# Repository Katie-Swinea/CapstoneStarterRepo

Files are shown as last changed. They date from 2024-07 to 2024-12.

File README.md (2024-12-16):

# Paper Wad Interceptor - Purple Team

## Executive Summary

It is a common problem that students that are currently in school lack interest in STEM subjects. This is a problem for society as it hinders innovation and
discovery in future generations. It also negatively affects current infrastructure and systems in place. Without students who are interested in these fields
of study and existing structures, failures in infrastructure and government programs could occur. This project aims to spark students interest in STEM
fields and applying the principles to existing infrastructure.

The goal of this project is to replicate a missile defense system to interest children in STEM, specifically the department of defense. This is done be
scaling the original problem down to a smaller area. This scale down is proposed as a paper wad interceptor in a classroom. However, this project is
incredibly ambitious for the time provided to the team. Due to this, the project was then simplified further. Instead of a paper wad that could come from
anywhere in a large classroom, the object being tracked was replaced with a plastic practice golf ball. The golf ball will be coming from a structure with
fifteen possible start point and two variable heights. The narrows down the possible trajectories to 30. The space was also contained to a 64 inch by 78
inch rectangle. This resulted in a project focused on small object tracking with the added challenge of the object's material properties and speed. Since
the project was already being scaled down, the project was also turned into a competition between two teams. 

## Capabilities

This system is able to accurately detect, track, and aim at the incoming golfballs on the gameboard. It has been designed to mitigate false detections as much as possible. It is able to accurately intercept the
ball a significant percent of the time.

## Salient Outcomes

The team has learned about tracking smaller objects through this project. The object's size was not an issue the team anticipated to be such a challenge.
While there are several sensors that are capable of tracking objects, very few can reliably track a small object such as a plastic golf ball. This issue was
highlighted even further with the limitation sensors that can detect plastic. Research shows that vision detection is the most reliable and used technology
for small object tracking. This was an outcome the team was not expecting from the project. This difficulty was something the team had to overcome and learn
from to achieve the goal of the project.

## Project Demonstration & Images

The experimental analysis of this repository has several pictures of the capabilities of this project. The final presentation also has a video of the interceptor tracking and hitting the golfball.

## About Us

### Team

Garrett Armstrong: Electrical Engineering major who focused on the power for the system created.

Savannah Metlzer: Electrical Engineering major who focused on providing the signal conversions and aiming coordinates for the motors.

Jonathan Neal: Electrical Engineering major who focused on interfacing the extra lights and sound into the system.

Finlay Patoto: Computer Engineering major who focused on the processor and basic mathmatical calculations from the sensor data.

Katie Swinea: Computer Engineering major who focused on the computer vision algorithms to detect the object and convey the sensor data.

Kevin Ulrich: Computer Engineering major who focused on the research and calibration of a sensor to detect the object.

### Faculty Supervisor

The team's faculty supervisor was Dr. Jesse Roberts. The team's supervisor then became Micah Rentschler for the second semester.

### Stakeholders

The customer is Devcom who also created and proposed the project and competition.

### Recognitions

The team wants to acknowledge the contributions of the partnered Mechanical Engineering team. The team consists of: Ishak Lamei, Samuel Rainey, Steven
Tucker, and Austin Williams. The team would also like to thank Cooper Nelson for helping the team test different sensor options before ordering, Ethan Dixon who was a source of moral support through out the
project, and Adam Morrow who was on the other team, but helped us finish construction of the gameboard and let us bounce ideas off of him.

## Repo Organization

The timeline that was used as a template for the team's more detailed timeline and this README are present in main with the following repository.

### Reports

This repository contains the original Project Proposal, the revised Proposal, the Conceptual Design and Planning draft, and the final Conceptual Design and
Planning document. All of these files are included as pdf documents. There are also several markdown files containing instructions for furture documents. 
These include the Lessons Learned and Acquired, Experimentation, Final Presentation, and Poster Documents. Lastly, there is another repository called Poster
Template present.

### Documentation

This repository contains several repositories inside of it. One is 3D models which will include all the final designs for 3D models. Next is Electrical which
contains two repositories called PCB and Schematics. PCB will house all final PCB designs. Schematics will house all final designs for wiring schematics. The
Images repository is used to store the images of the final project. The team has also used this repository to house all images used in documentation. Meeting
Minutes are included in a repository here as well. Signoffs contains the approved final design of each subsystem. 

### Software

This repository contains the necessary software and designed software for the project. All of theses softwares are already uploaded to the appropriate hardware.

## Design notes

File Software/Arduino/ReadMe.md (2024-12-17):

# Code for the Arduino

This is the code that was developed for the competition. It is used to control the stepper motors in order to position and aim the interceptor towards the incoming 
golfball. It uses the information from the jetson nano sent via I2C communication. The information is a byte that contains the x and y position for the motors and a 
fire bit for the solenoid to launch the projectile at the golfball.

This software uses header files ezButton.h, AccelStepper.h, Wire.h, and avr/wdt.h for proper interfacing with the stepper motors, limit switches, and solenoid to 
ensure the interceptor moves properly.

This software can be uploaded on the adruino by connecting it to a computer with the code and uploading it when the adruino is ready to accept a new upload of code. 
Ensure the arduino and computer are connected to the same ground. This version of the code is currently uploaded on the arduino.

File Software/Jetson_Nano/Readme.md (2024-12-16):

# Code for the Jetson Nano

This is the code that was developed for the competition. It includes the integration of the jetson nano with the real sense camera including the color map and paramter
adjustments. The code also includes the image processing, false detection handling, frame storage, velocity and acceleration calculations, and trajectory predictions.
The location of the ball and predictions are sent to arduino via I2C. The code also include the buzzer noise for firing and light's pattern and the pause switch
functionality with the switches input into the nano being used to temporarily stop the program.

The code uses the opencv library, the real sense library, and the jestson's gpio pin interface. It also requires other libraries for functionality like the time, 
numpy, typing for tuple, subprocess, sys, threading, os, smbus2, time, and math. These are used for specfic operations and calculations.

This software can be uploaded on the jeston nano via a USB as it it. It can be set to run when the jetson nano is turned on with a simple program already uploaded on
the jeston nano. Use a monitor to see the jeston nano console and change the program that runs on start up.

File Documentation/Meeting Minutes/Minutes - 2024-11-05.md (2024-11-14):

# Capstone II Team 5 Week 11 (11/04 – 11/08)

### 11/05 @ 11:00 AM – 11:48 AM

### Attendance: Everyone + DEVCOM + Mechanicals

## Updates:

Garrett: Finished experimental analysis for power system

Finn: Started testing values for lookup tables

Katie: Refined image detection to reduce noise and verified correct communication with code elsewhere on Jetson.

Ross: Fixed buzzer

Savannah: Started testing values for lookup tables

Kevin: Helped find fix for dart jamming problem

## Future Tasks:

Garrett: Work on lookup tables for converting coordinates from camera to real life.

Finn: Work on lookup tables for converting coordinates from camera to real life.

Katie: Work on lookup tables for converting coordinates from camera to real life.

Ross: Finish experimental analysis for extra system

Savannah: Work on experimental analysis for arduino system

Kevin: Work on experimental analysis for camera system

## Discussions/Decisions:

Discussed other team's sensor posts and talked about the 6 foot rule for our team.

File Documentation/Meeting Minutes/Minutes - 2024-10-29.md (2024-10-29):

# Capstone II Team 5 Week 10 (10/28 – 11/1)

### 10/29 @ 11:30 AM – 12:06 PM

### Attendance: Everyone

## Updates:

Garrett: Completed housing.

Finn: Developed working prototype of calculations for coordinates for aiming.

Katie: Worked with image detection to further reduce noise.

Ross: Worked on integration of buzzer.

Savannah: Finished wiring up gameboard

Kevin: Remounted camera to the front to avoid image detection noise from gun.

## Future Tasks:

Garrett: Continue writing drafts of final reports.

Finn: Continue developing the calculations code with jetson.

Katie: Continue refining image detection to reduce noise and verify correct communication with code elsewhere on Jetson.

Ross: Continue fixing buzzer.

Savannah: Work on converting coordinates from image detection to real life coordinates with aiming turret.

Kevin: Help develop code for calculations and image detection.

## Discussions/Decisions:

Discussed progress and verified future tasks to continue finishing up subsystems for minimal functioning prototype.

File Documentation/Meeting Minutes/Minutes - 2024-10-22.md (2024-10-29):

# Capstone II Team 5 Week 9 (10/21 – 10/25)

### 10/22 @ 11:00 AM – 11:46 AM

### Attendance: Everyone + Mechanicals + DEVCOM

## Updates:

Garrett: Helped finalize wiring in finished housing.

Finn: Helped finalize wiring in finished housing. Also worked with aiming code and positioning.

Katie: Fixed image detection noise problem.

Ross: Helped finalize wiring in finished housing.

Savannah: Worked on the gameboard.

Kevin: Taped out the positions of sensor posts and other important positions on the gameboard. Camera mount finished

## Future Tasks:

Garrett: Start writing paper for experimental analysis and final paper.

Finn: Work on calculation with coordinates from image detection.

Katie: Refine image detection with testing.

Ross: Integrate buzzer into housing and the rest of the subsystems.

Savannah: Finish the setup of the gameboard. (Stringing up the rest of the wires and reset the anchor points for the wires to set in.

Kevin: Determine final position of the camera.

## Discussions/Decisions:

Discussed progress with mounting, housing, Arduino code, Jetson code, timing, and optimization. Also discussed possibility of the removal of the 6-foot rule. talked about making a compromise package for the other team. Verified that there are no changes to the gameboard.

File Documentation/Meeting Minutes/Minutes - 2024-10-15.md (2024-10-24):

# Capstone II Team 5 Week 8 (10/14 – 10/18)

### 10/15 @ 11:00 AM – 11:27 AM

### Attendance: Everyone

## Updates:

Garrett: Finalized wiring within the housing.

Finn: Launcher fires and aims with arduino through Jetson nano.

Katie: Further implemented the multiframe storage for image detcection.

Ross: Finished layout of internal units and attached to base of housing.

Savannah: Helped with arduinos firing with communication with Jetson.

Kevin: Waiting for housing and camera mount to be completed.

## Future Tasks:

Garrett: Waiting for mechanicals to finish walls of housing.

Finn: Fine tune the aiming code.

Katie: Fix image detection noise problem.

Ross: Waiting for mechanicals to finish walls of housing.

Savannah: Help fine tune the aiming code and finalize gameboard.

Kevin: Waiting for mechanicals to finish walls and camera mount.

## Discussions/Decisions:

Discussed and set deadlines for remaining tasks till end of semester.

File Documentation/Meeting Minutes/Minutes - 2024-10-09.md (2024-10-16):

# Capstone II Team 5 Week 7 (10/07 – 10/11)

### 10/09 @ 11:00 AM – 11:43 AM

### Attendance: Everyone + Mechanicals + DEVCOM

## Updates:

Garrett: Finalized wiring between different subsystems.

Finn: Jetson is now communicating with arduinos.

Katie: Began implementation of multiframe storage.

Ross: Finalized mapping out systems into the housing.

Savannah: Helped communication between arduinos and Jetson.

Kevin: Recieved USB C cable.

## Future Tasks:

Garrett: Wired different systems together through the housing.

Finn: Get launcher to fire with the arduinos.

Katie: Finish multiframe storage and prepare for testing.

Ross: Put housing together.

Savannah: Help get launcher to fire with arduinos.

Kevin: Discuss camera mount with mechanicals.

## Discussions/Decisions:

Discussed with DEVCOM some questions regarding the gameboard and clearing up some finer details and misunderstandings.

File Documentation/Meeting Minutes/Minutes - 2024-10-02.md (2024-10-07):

# Capstone II Team 5 Week 5 (10/30 – 10/04)

### 10/02 @ 11:00 AM – 11:32 AM

### Attendance: Everyone + Mechanicals

## Updates:

Garrett: Mapped out subsystems within 1 cubic foot box.

Finn: Researched communication protocols for link between Jetson and arduino

Katie: Determined method for testing timing and gathering frame data.

Ross: Mapped out subsystems within 1 cubic foot box.

Savannah: Helped mechanicals swap from their arduino to our arduino

Kevin: Helped map out subsystems within 1 cubic foot box.

## Future Tasks:

Garrett: Continue mapping out subsystems in box. Ordered new parts for mechanical subsystem change.

Finn: Implement communication with arduinos.

Katie: Implement multi-frame data storing. Start testing actual timing processes.

Ross: Continue mapping out subsystems in box.

Savannah: Help implement communication with Jetson.

Kevin: Submit BOM for new, longer usb c cable.

## Discussions/Decisions:

Discussed housing layouts for fitting each subsystem into required space.

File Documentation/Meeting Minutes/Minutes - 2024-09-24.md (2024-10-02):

# Capstone II Team 5 Week 5 (9/23 – 9/27)

### 09/24 @ 11:00 AM – 11:45 AM

### Attendance: Everyone + DEVCOM + Mechanicals

## Updates:

Garrett: Fully integrated with each subsystem besides mechanical.

Finn: Worked on integration with buzzer, pause switch, and auto-launching scripts.

Katie: Reexamined image detection plan (performance, timing, etc.)

Ross: Helped integrate extras system with power and jetson.

Savannah: Got Arduino in.

Kevin: Helped with integration with extras subsytem and jetson nano.

## Future Tasks:

Garrett: Start configuring layout for fitting everything together.

Finn: Integrate with the rest of the subsystems and start configuring layout.

Katie: Continue working on more exact timing for the image detection.

Ross: Start configuring layout for fitting everything together.

Savannah: Work with mechanicals to integrate between launcher and jetson.

Kevin: Help configure layout for camera subsystem

## Discussions/Decisions:

Talked with DEVCOM about image detection progress and developments. Also discussed game board changes such as the fishing hook for sliding down the fishing line better.

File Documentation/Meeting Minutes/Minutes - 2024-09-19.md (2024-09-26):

# Capstone II Team 5 Week 4 (9/16 – 9/20)

### 9/19 @ 11:30 AM – 12:00 PM

### Attendance: Everyone

## Updates:

Garrett: Started wiring and troubleshooting power subsystem.

Finn: Got current image detection script working with camera and jetson nano

Katie: 

Ross: Assembled extras and pause switch subsystem.

Savannah: Submitted BOM and talked with mechanicals to figure out how to integrate with the rest of the subsystems.

Kevin: Helped get current image detection working off of Jetson Nano and camera.

## Future Tasks:

Garrett: Continue assembling power subsystem and start integration testing.

Finn: Get Jetson Nano to auto run scripts and show status.

Katie: Plan timelines for internal deadlines to ensure all subsystems are getting integrated on time.

Ross: Integrate extras subsystem with power subsystem and Jetson.

Savannah: Waiting on parts.

Kevin: Help integrate Jetson with other subsystems.

## Discussions/Decisions:

Discussed housing and made sure all subsystems would fit within the specs and constraints of the rules and what the mechanicals are working on.

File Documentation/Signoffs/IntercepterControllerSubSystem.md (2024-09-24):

# Interceptor Controller Subsystem

## **Function:**
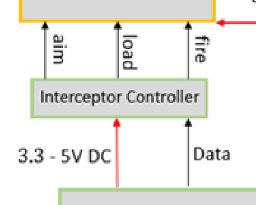
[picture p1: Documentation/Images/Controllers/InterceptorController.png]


Figure 1: Interceptor Controller Subsystem

The goal of this subsystem is to activate the position motors and firing mechanism within the mechanical system, maintain safe firing speed, as well as alleviate some of the coding within the processor. 

## **Constraints:**

|No.|Constraint|Origin|
|--|---|---|
|1|The Interceptor Controller shall move firing mechanism to 1 of 30 pre set locations |Conceptual Design|
|2|Must communicate with processor| Conceptual Design |
|3|Shall receive 5V power supply from processor| Conceptual Design|
|4|Must change direction of the motors in the Mechanical's section |Conceptual Design|
|5|Must maintain safe firing speed and distance|Conceptual Design/Rule Book|
|6|Must change position before incoming object enters the "kill zone"| Conceptual Design|

1.	Using the sensor data analyzed by the processor the arduino activates the 2 position motors to move to 1 of 30 set positions.
2.	After completing the movement to the desired position, and the projectile is within set "kill zone", the firing mechanism is engaged firing only one shot.
3.	Using the 5V pin on the processor to power the adruino.
4.  To be able to move to the correct coordinates the motors need to move in either direction along the x and y axis.
5.  Per Devcom rule books the projectile must be fired at a safe speed and stay within a distance of 6ft *this speed will be found by the ME team*
6.  Based off calculations made with the dimensions of the game board it will take the projectile approximately 1.95 seconds to 7.4 seconds to travel down the line given the two different height points. However, after subtracting the worst-case scenario with sensing, processing, and travel time this leaves 1.6 seconds for the firing mechanism to move into position and fire at the object before collision.

## **Buildable Schematics:**

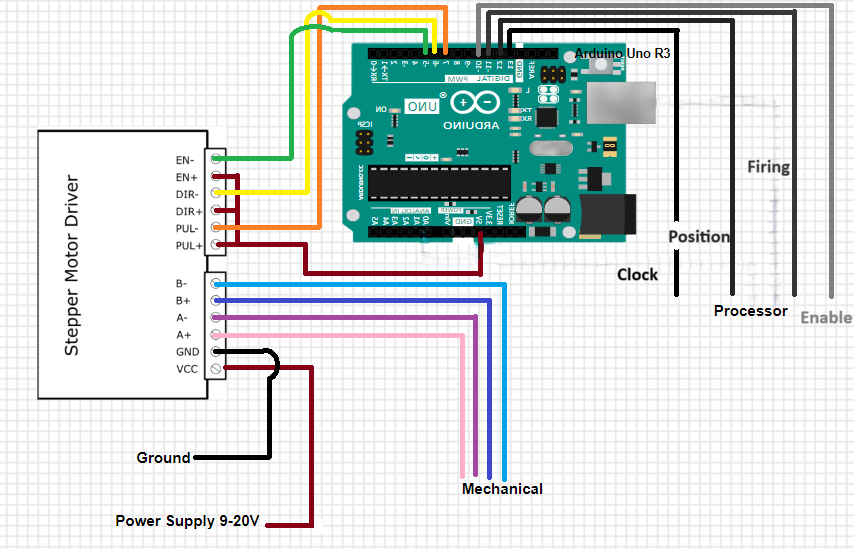
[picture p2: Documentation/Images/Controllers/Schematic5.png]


Figure 2: Buildable Schematic

## **Analysis:**

Stepper Motor Integration:

The stepper motor driver converts a pulse signal into a precise position and can also make the rotation of the motor bidirectional. With this function and the orientation of the motors we are able to create an x and y axis for the firing mechanism to move on. This allows 30 set coordinates to be programmed for possible incoming attacks. This component was pick by the Mechanical Engineering portion of our team, however, it is important to this subsystem because of its direct integration within the Arduino. Through GPIO communication, as stated above, the Arduino UNO R3 commands the stepper motor driver to adjust the interceptor's position, aligning it with the golf ball's predicted path. Real-time trajectory data calculated by the processor is sent to the Arduino that will guide its precise motor movements, ensuring accurate interception. After firing is completed the stepper motor will be put back into a zero position. While it is in its zero position, the processor can count how many steps the motor takes to determine the correct aiming position [6].

Arduino Intergration:

*Motor Integration*

As stated before the stepper motor drive given was picked by the ME team. This component was picked through testing and consideration of use by them. The Arduino UNO R3 seamlessly integrates with the TB6600 Stepper Motor Driver to control the interceptor's aiming mechanism [7]. With that being said an Arduino was picked to be used within this subsystem to control the driver. Through research it is found to be the most commonly used device to pair with the stepper motor driver and with a large data base of research, experiments, and recommendations. This also allows the team to alleviate some of the coding within the processor making it easier to trouble shoot problems, breaks up coding assignments, and allows for specific testing with the ME team to fine tune the speed and positions.The arduino will need to set the motors to move between 200 and 600 RPMs [9] to allow ample time for firing. At 200 RPMs it allows 3 full rotations per second, however, the position only has a range of 180 degrees so this makes it 6 half rotations per second. If we find this is not quick enough through testing we can at max triple this making it 18 half rotations per second. The motor used for the firing mechanism runs at 10,000 RMPs and will be plenty fast enough to hit the object in time. 

*Processor Integration*

The arduino will also be communicating with the processors Jetson Nano through the SPI pins. Pin D13 (SPI serial clock output) will be used as the clock between the two. Pin D12 (SPI Main In Secondary Out) will allow the processor to send data to the arduino as to which line the projectile is coming from. The arduino will then determine which of the 30 positions it is and initiate the position motors to move accordingly. Pin D11 (SPI1 Main Out Secondary In) after the position is in place a signal will be sent for a ready fire and then will load the ammunition into the barrel and fire. After this the mechanism will return to "zero position" or starting state and is ready for the next target. Pin D10 will be used as the Enable pin.

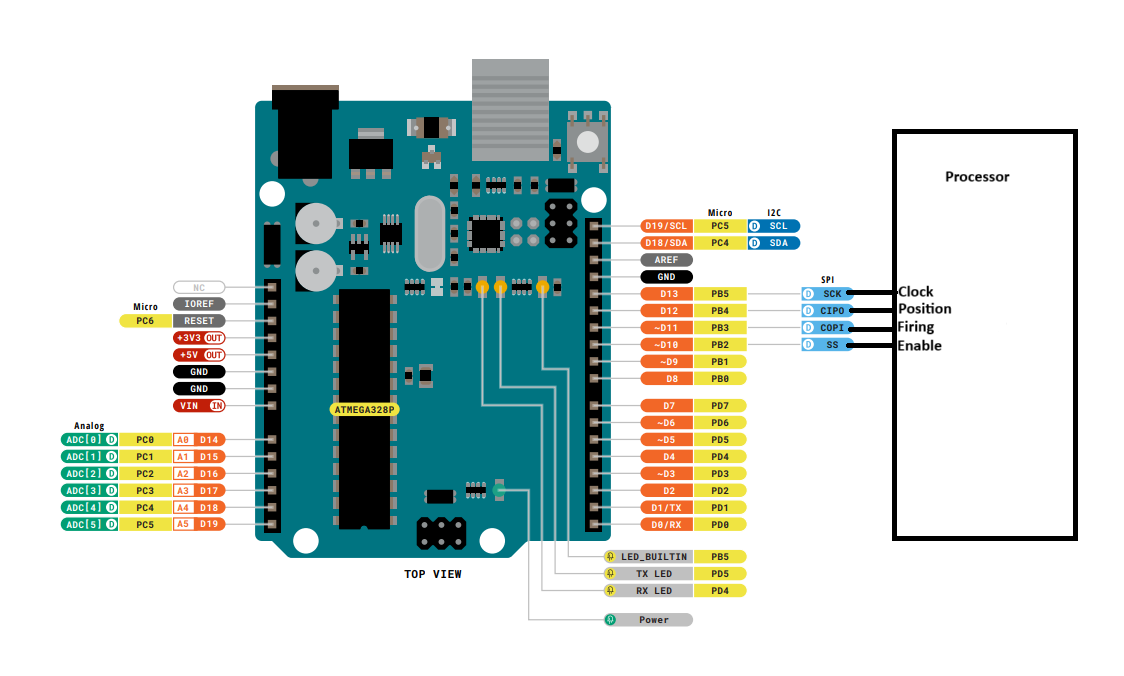
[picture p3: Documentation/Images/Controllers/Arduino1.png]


Figure 3[1]

## **Bill of Materials:**

|Device|Description|Used in which subsystem|Part Number| Manufacturer|Quantity|Price|Total|
|---|---|---|---|----|----|----|----|
| Arduino UNO R3 |converts analog data to digital inputs to move motors|Interceptor Controller Subsystem|A000066| Arduino|2|$27.60|$55.20|
|TB6600 Stepper Motor Driver|Regulates current and keeps from going reverse bias, and divides rotation into equal steps|Interceptor Controller Subsystem & Mechanical Subsystem|TB6600|DFRobot|0||purchased by ME team|
| | | | | | |Final Total|$55.20|

## **References:**
[1] Arduino, https://docs.arduino.cc/resources/pinouts/A000066-full-pinout.pdf (accessed Apr. 17, 2024). 

[2] Arduino, https://docs.arduino.cc/resources/schematics/A000066-schematics.pdf (accessed Apr. 17, 2024). 

[3] Arduino, https://docs.arduino.cc/resources/datasheets/A000066-datasheet.pdf (accessed Apr. 17, 2024). 

[4] Admin, Technology tutorials, https://toptechboy.com/arduino-tutorial-37-understanding-how-to-control-dc-motors-in-projects/ (accessed Apr. 17, 2024). 

[5] R. Sawkare, “Arduino Uno R3 with l293d motor driver,” Medium, https://vayuyaan.medium.com/arduino-uno-r3-with-l293d-motor-driver-550c4a65f612 (accessed Apr. 17, 2024). 

[6] “TB6600 Stepper Motor Driver,” Bulkman, https://bulkman3d.com/wp-content/uploads/2019/06/TB6600-Stepper-Motor-Driver-BM3D-v1.1.pdf (accessed Apr. 8, 2024).

[7] “TB6600 Stepper Motor Driver,” DFRobot, https://www.dfrobot.com/product-1547.html (accessed Apr. 8, 2024).

[8] S. Hall, Devcom. Devcom, 2024. S31 Paper Wad Interceptor Challenge 2024, Rulebook, (accessed Apr. 8, 2024).

[9] K. Godiyal, “Guide to nema 17 Stepper Motor Dimensions, wiring pinout,” eTechnophiles, https://www.etechnophiles.com/guide-to-nema-17-stepper-motor-dimensions-wiring-pinout/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,this%2C%20the%20recommended%20speed%20range%20is%20200-700%20RPM. (accessed Sep. 2, 2024).

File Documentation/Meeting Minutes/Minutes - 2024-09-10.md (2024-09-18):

# Capstone II Team 5 Week 3 (9/9 – 9/13)

### 9/10 @ 11:00 AM – 11:30 AM

### Attendance: Everyone + Mechanicals + DEVCOM

## Updates:

Garrett: Got power system signoff and submitted BOM.

Finn: Got image detection working better with depth camera + color masking.

Katie: Started preliminary timing chart. Waiting for mechanicals timing.

Ross: Waiting for parts to arrive. Got signoff.

Savannah: Got subsystem signed off.

Kevin: Worked on image detection with Finn

## Future Tasks:

Garrett: Waiting for parts to arrive.

Finn: Work on getting Jetson Nano ready with Linux and python/libraries.

Katie: Improve image detection with depth camera.

Ross: Solder system together.

Savannah: Submit BOM and keep in touch with mechanicals.

Kevin: Improve image detection with depth camera.

## Discussions/Decisions:

Talked to DEVCOM and discussed current progress with each subsystem.

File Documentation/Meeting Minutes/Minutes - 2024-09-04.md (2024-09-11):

# Capstone II Team 5 Week 2 (9/2 – 9/6)

### 9/4 @ 11:58 AM – 12:26 PM

### Attendance: Everyone + Mechanicals

## Updates:

Garrett: Continued work on detail design/signoff.

Finn: Got processing system signoff.
      Helped improve image detection with depth camera.

Katie: Helped improve image detection with depth camera.

Ross: Got extras subsystem signoff.

Savannah: Refined subsystem prepared questions for mechanicals 

Kevin: Made rough draft of image detection with depth camera.

## Future Tasks:

Garrett: Continue work on detail design/signoff.

Finn: Improve image detection with depth camera.

Katie: Improve image detection with depth camera.

Ross: Submit BOM to get parts ordered.

Savannah: Work with what mechanicals gave us to elaborate on detail design/signoff.

Kevin: Improve image detection with depth camera.

## Discussions/Decisions:

Talked with the mechanical team about the launcher base. We made sure that the mechanical team was on the same wavelength as us in terms of what data was being sent between the two teams.

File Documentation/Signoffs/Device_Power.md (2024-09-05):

# Device Power Subsystem

**Function:**

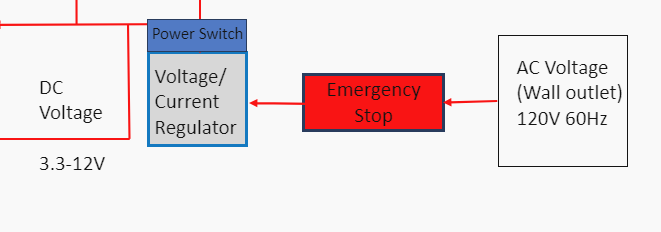
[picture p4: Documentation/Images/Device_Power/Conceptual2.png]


Figure 1: Device Power Subsystem

The goal of this subsystem is to convert AC power from the wall outlet to DC power, and then distribute that power to the different device systems.  

**Constraints:**

| NO. | Constraint | Origin |
|-----|---|---|
| 1 | The power system shall be controlled by an emergency stop which will de-energize the mechanical system. This will shut off the motors which will not allow any projectiles to be fired. This will only be used if the system threatens peoples safety |Conceptual Design |
| 2 | The system shall convert wall outlet AC voltage to up to 24 volts at up to 20 amps for the mechanical system. This includes two DC motor controllers which requires 9-48 volts at 5 amps and the DC motor which will receieve anywhere from 12-24 volts at 10 amps |Conceptual Design |
| 3 | The system shall convert wall outlet AC voltage to up to 5 volts at up to 5 amps for the proccesor system, which requires 5 volts at 4 amps, relay coil which requires 5 volts as a high impendence input and the extra subsystem which requires 5 volts at 0.8 amps. |Conceptual Design |
| 4 | The system shall be controlled by a power switch |Conceptual Design |

<sup>1</sup> The power system shall be controlled by an emergency stop which will de-energize the mechanical system. This will shut off the motors which will not allow any projectiles to be fired. This will only be used if the system threatens peoples safety  [Conceptual Design]

One of the requirements in the rulebook, given to us by the customer, is that the interceptor needs to have an emergency stop that de-energizes the interceptor. This emergency stop will cut power from the AC-DC convertor for the mechanical system to the motors themselves which will de-energize the interceptor. This system will only be used as a last case option if the interceptor threatens peoples safety. 

<sup>2</sup> The system shall convert wall outlet AC voltage to up to 24 volts at up to 20 amps for the mechanical system. This includes two DC motor controllers which requires 9-48 volts at 5 amps and the DC motor which will receieve anywhere from 12-24 volts at 10 amps  [Conceptual Design]

The entire mechanical system will need up to 24 volts at 20 amps (480 watts). This will power one DC motor and two DC motor controllers. The DC motor requires 12 to 24 volts depending on the amount of RPMS required to fire the projectile at a specfic speed. The two DC motor controllers require anywhere from 9-48 watts depending on which type of motor it will control. The selected supply will supply 24 volts with a ripple percentage of +/- 5% [2]. This means it will supply up to 25.2 volts or as low as 23.8 volts. This is not an issue for either system as the controller can handle a much broader range and the motor will not be recieveing a max voltage as the mechanical team will limit it's voltage to allow the required RPM. 

<sup>3</sup> The system shall convert wall outlet AC voltage to up to 5 volts at up to 5 amps for the proccesor system, which requires 5 volts at 4 amps, relay coil which requires 5 volts as a high impendence input and the extra subsystem which requires 5 volts at 0.8 amps. [Conceptual Design]

The system will need to power the extra subsystem, relay coil and the processor system. The extra system is a light and buzzer PCB. This system will be responsible for powering the lights on that PCB. There are current and voltage limiting resistors included on the board that will limit the supply voltage to the required voltage for the LEDS and allow them to run on 5 volts with head room for spikes. There are 2 types of LEDs, a red type which needs 0.05 amps and a green type which needs 0.02 amps. There will be 10 of each for a total of 0.7 amps. The processor system will be the Jetson Nano Devolper kit which will take 5 volts at 4 amps through the barrel jack connector. This supply will also need to power the relay coil which will require a 5 volt high impendence input. The power supply that will be used will be a 5 volt 10 amp power supply[1]. This power supply will have plenty of excess power head room to power every device it will need to power.

<sup>4</sup>  The system shall be controlled by a power switch.  [Conceptual Design]

The system will be controlled by an on/off switch. This switch will allow the wall power to be connected or disconnected from each system that this subsystem powers.  

## Buildable schematic 

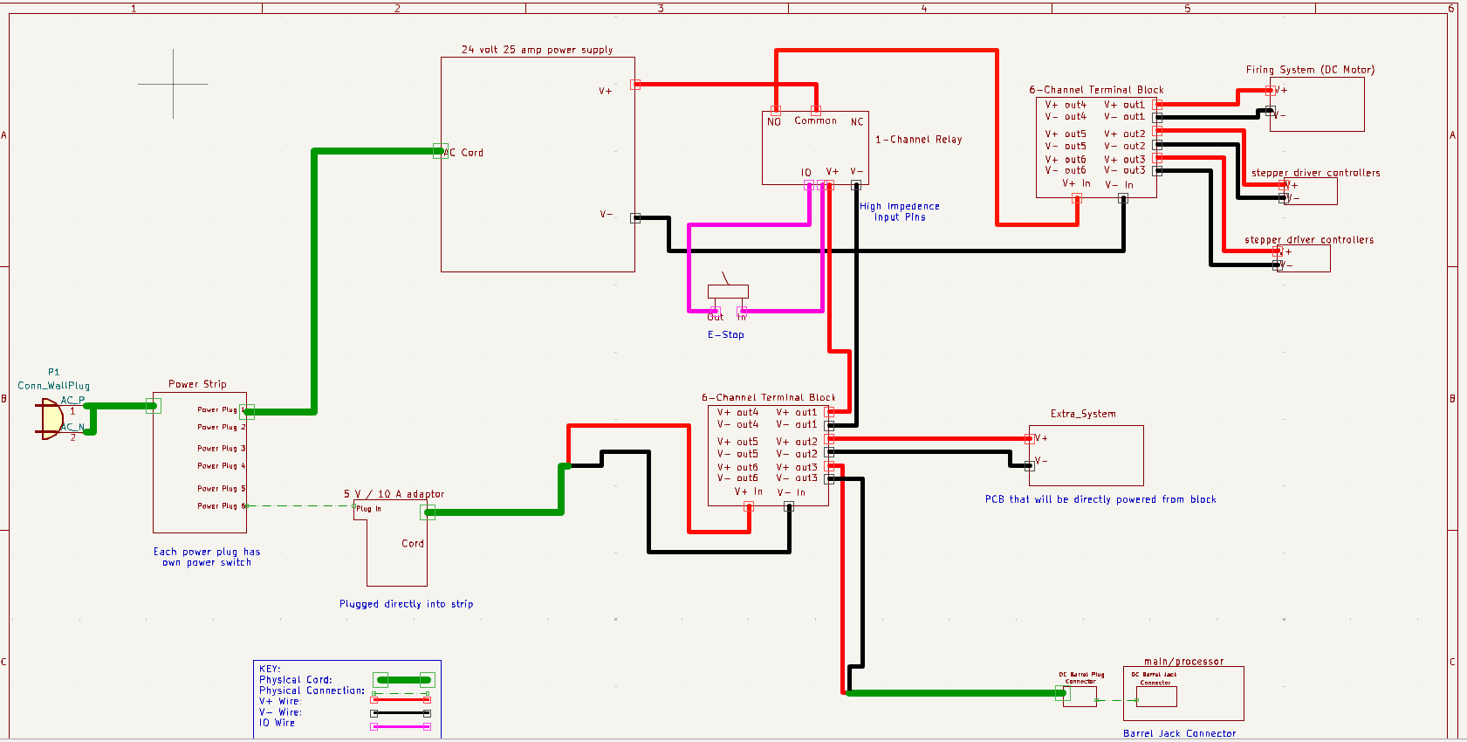
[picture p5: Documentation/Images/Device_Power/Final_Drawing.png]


*power subsystem buildable schematic*

The wires used for the mechanical system, extra system and relay coil will be 8 AWG wire as it will completely encapsulate the max requirment of 24 volts at 25 amps [8].

The input wire to the Jetson Nano will be a Barrel Jack connector cord rather than a micro-USB becuase the image processing system has ran it's calculations with the processor receiving this specfic draw. This wire will be rated to handle at least 5 volts at 4 amps as that is what the Jetson Nano will be drawing [7].

Both power supplies will have it's output split using a terminal block that will act as power bus to every system that draws power from it [6].

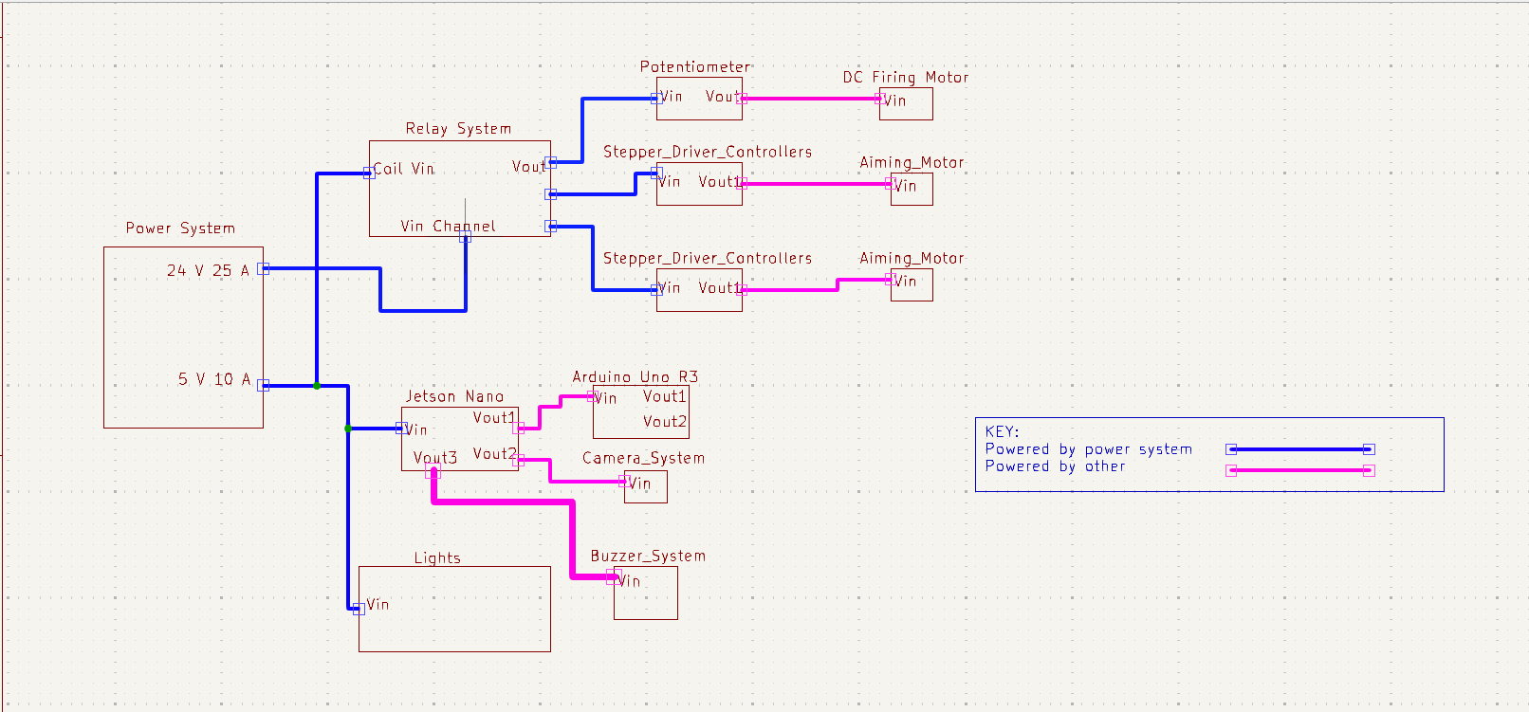
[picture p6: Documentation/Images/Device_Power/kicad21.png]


*Entire project power schematic*

This is to show the power system is supplying power to everything it needs to power in order to accomplish everything this project is required to do. The power system will just supply power to three motors, the relay system, the processor and the extra system. Every other componet will be powered by another componet. 

## Analysis

| System | Voltage | Current | Power | 
|---|---|---|---|
| Mechanical | 24 Volts | 20 Amps  | 480 Watts |
| Processor | 5 Volts | 4 Amps | 20 Watts |
|Emergency | 5 Volts | 0.7 Amps | 3.5 Watts | 
|Total |  | | 503.5 Watts |

The above table details the different power draws that is required from this system. 

### Mechanical:

This power system will supply power to three main componets of the mechanical system. These componets are the firing mechanism's DC motor, and two stepper driver controllers that will control the aiming of the interceptor. The DC motor has a maximum voltage requirement of 24 volts with an amperage draw of 10 amps. It will be lowered to allow the correct RPM of the motor so the projectile does not exced the specified speeds. At worst case, this means the power draw of this system will be:

<p align="center">DC Motor Power Draw: (24 volts) * (10 amps) = 240 watts</p>

The two stepper driver controllers have a voltage requirment between 9 and 48 volts. 24 volts will be given to this system so it can be powered by the same system. It's amprage draw is between 0-5 amps. The amperage of these controllers depends on the amount of power the actual motors need, so this system must be able to produce the maximum current so the motors can recieve the maximum current if needed. This means the total power draw of both controllers will be:

<p align="center">Single Controller Power Draw: (24 volts) * (5 amps) = 120 watts</p>

<p align="center">Total Controller Power Draw: (120 watts) + (120 watts) = 240 watts</p>

This places the maximum power draw of the entire system at:

<p align="center">Total Power draw of the Mechanical System: (240 watts) + (240 watts) = 480 watts</p>

To acomplish the total power draw required, this system will utilize a power supply capable of supplying 600 watts of power[2]. This will give the system plenty of head room in powering the three componets as it will supply 120 more watts then is required.

### Extra:

The extra subsystem will be a PCB board that will be controlled by the processor system. This board will have 2 types of LEDs, and there will be 10 of each. The first type will be a green LED that will require 3 volts and 20 mAmps. It will receive 5 volts from the supply and will be limited to 3 volts using a 100 ohm resistor. There will be 10 of these so the total current draw will be:

<p align="center">Total current draw of the green LEDS: (10 * 0.02) = 0.2 amps  watts</p>

The second type will be a red led which will require 2.5 volts and 0.05 amps. It will also receive 5 volts from the supply which will be limited by a 50 ohm resistor. There will also be 10 of these so the total current draw will be:

<p align="center">Total current draw of the red LEDS: (10 * 0.05) = 0.5 amps  watts</p>

These means the total current draw and thus the total power draw of this system will be:

<p align="center">Total current draw of all LEDS: 0.2 + 0.5 = 0.7 amps  watts</p>

<p align="center">Total Power draw of all LEDS: 5 volts * 0.7 amps = 3.5 watts  watts</p>

This system will be powered by the 5 volt 10 amp supply that will also power the processor system and relay coil. 

### Processor:
The processor system will be controlled by a Jetson Nano developer kit. This Jetson Nano requires a voltage of 5 volts and an amperage draw of 4 amps. The total power draw of this system will then be:

<p align="center">(5 volts) * (4 amps) = 20 watts</p>

To acomplish this power draw, the system will utilize the 5 volt 10 amp power supply that will also be powering the extra system and relay coil[1]. 

### Emergency Stop

In order for the emergency stop to properly de-energize the entire mechanical system, one switch must be able to operate on three seperate circuits. The way this system will accomplish this is through the use of a 1-channel relay componet. This one channel relay takes a 5 volt input to charge the coil. It will power this coil using the 5 volt 10 amp supply that is powering the extra system and Jetson Nano[1]. 

The single output of the 24 volt 25 amp power supply will be connected to the common input of the relay and there connected output will connect to the NO (normally open) input. This will cause the 24 volt signal to output whenever the coil is connected to the 5 volt input. This means that whenever the emergancy stop is not being pressed, it will output the 5 Volt signal to the relay, closing the NO contact allowing the mechancial system to become powered. When the emergancy stop is pressed, it will disconnect the 5 Volt signal, causing the NO contact to disconnect, severing the power to the mechanical system. This is the safer of the options becuase if the emergancy stop is messed up and no power can get through, the mechanical system will stay off. [4][5]

### Total Power

To achieve everything this system is required to do, the total power draw of this system will be:

<p align="center">(480 watts) + (3.5 watts) + (20 watts)  = 503.5 watts</p>

This will be accomplished by using two seperate power supplies. The first will supply a total of 600 watts and will power the Mechanical system [2]. The second will supply a total of 50 watts and will power the emergency system, Jetson Nano and the relay coil[1].

<p align="center">(600 watts) + (50 watts) = 650 watts</p>

The total supplied power of 650 watts will completely encapsulate the required wattage of 503.5 watts, and will allow the system to function correctly and accurately.

### Power Switch 

To accomplish the power switch constraint this system will utilize a power strip. This power strip will have six seperate plug ins each with it's own power switch. This system will utilize 2 of the six plugs as there are 2 power supplies being used in this system. The power strip selected is rated for 1875 watts of power which will comfortably encapsulate the 2 supplies being utilzed as the maximum power draw for this system is 503.5 watts. [3]

## BOM
|Item Name | Description | Subsystems | Part Number | Manufacturer | Quantity | Price | Total |
|---|---|---|---|---|---|---|---|
|CCCEI Metal Power Strip Individual Switches 6 Outlets | 6 plugin power strip with 6 switches | Mechanical, Extra, Processor | B08HYLW3GX | CCCEI | 1 | 16.99 | 16.99 |
|Emergency stop switch | Switch will cause the relay to disconnect the power to the Mechanical system | Mechanical | B079FKJG26 | API Electric | 1 | 9.99 | 26.98 |
|5V 10A Power Supply Adapter | Power supply rated for 5 volts and 10 amps | Processor, Extra | 	B07CMM2BBR | Aclorol | 1 | 19.99 | 46.97 |
|DC 24V 25A 600W Power Supply | 600 watt power supply | Mechanical | 	B0BKY78JDX | NUOFUWEI | 1 | 49.99 | 96.96 |
| 1-channel relay | Relay that will disconnect the power to the motors | Mechanical | B07DSZFLMQ | NOYITO | 1 | 8.99 | 105.95 |
| 6-channel terminal block | 6-channel power block to split power | All | B09D3BV22M | CZH-LABS | 2 | 12.99 | 131.93 |
| 16-AWG barrel jack connector | Barrel jack connector to power Jetson Nano | Processor | B07VW5VRX7 | SIOCEN | 1 | 6.99 | 139.92 |
| 8-AWG electrical wire | Electrical wire to hook up each system | Processor, Mechanical | B0BYJRDT19 | Beffkkip | 1 | 19.99 | 158.91 | 

## References 

[1] Amazon.com: ACLOROL 5V 10A 50W power supply 100v-240v AC to DC Adapter 5V 10 AMP switching Converter 5.5x2.1mm plug for WS2811 WS2812B WS2813 5V led strip pixel lights : Tools & Home Improvement, https://www.amazon.com/Aclorol-100V-240V-Switching-Converter-5-5x2-1mm/dp/B07CMM2BBR (accessed Apr. 29, 2024). 

[2] Amazon.com: New Version DC 24V 25A 600W switching power supply adapter 110V AC to 24V DC converter power supply transformer for 24 Volt Winch Car Jack Monitor CCTV security camera car stereo and more 24V device : Electronics, https://www.amazon.com/Version-Switching-Converter-Transformer-Security/dp/B0BKY78JDX (accessed Apr. 29, 2024). 

[3] Amazon, https://www.amazon.com/Individual-Switches-Protector-Appliances-Extension/dp/B08HYLW3GX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 (accessed Apr. 16, 2024). 

[4] “30A 1-Channel Relay Module,” Amazon, https://www.amazon.com/NOYITO-1-Channel-Optocoupler-Automation-Industrial/dp/B07DSZFLMQ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 (accessed Apr. 29, 2024). 

[5] APIELE 22mm NC red mushroom emergency stop push button switch 600V 10 amp XB2-01ZS: Amazon.com: Industrial & Scientific, https://www.amazon.com/a12082000ux0309-Mushroom-Emergency-Button-ZB2-BE102C/dp/B079FKJG26 (accessed Apr. 23, 2024). 

[6] “30Amp 48V 2x6 Position Terminal Block,” Amazon, https://www.amazon.com/OONO-Position-Terminal-Distribution-Module/dp/B09D3BV22M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 (accessed Apr. 29, 2024). 

[7] “DC Power Pigtail Cable,16AWG DC Barrel Plug Connector,” Amazon, https://www.amazon.com/Pigtail-Supply-Security-Adapter-Connector/dp/B07VW5VRX7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 (accessed Apr. 29, 2024). 

[8] 8 AWG Gauge Silicone Wire Electrical Cable, https://www.amazon.com/Silicone-Electrical-Cable%EF%BC%8810ft-Temperature-Resistant/dp/B0BYJRDT19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 (accessed Apr. 29, 2024).

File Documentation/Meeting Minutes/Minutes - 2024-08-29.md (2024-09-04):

# Capstone I Team 5 Week 13 (4/15 – 4/19)

### 8/29 @ 11:30 AM – 12:29 PM

### Attendance: Everyone 

## Updates:

Garrett: Waiting for review on power system.

Finn: Submitted new pull request for processing system.

Katie: Image processing got signed off.

Ross: Submitted updated pull request for extras system.

Savannah: Waiting for responses from mechanicals for be able to update pull request for interceptor controller

Kevin: Camera got signed off.

## Future Tasks:

Everyone: Keep working toward remaining signoff.

Katie, Kevin, Fin: Test/develop image processing algorithm.

## Discussions/Decisions:

Discussed what to ask mechanicals (timing, loading, mounting/housing, etc.). Waiting for response from DEVCOM for meeting times for SME meetings.

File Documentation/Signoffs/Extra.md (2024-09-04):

# Extra

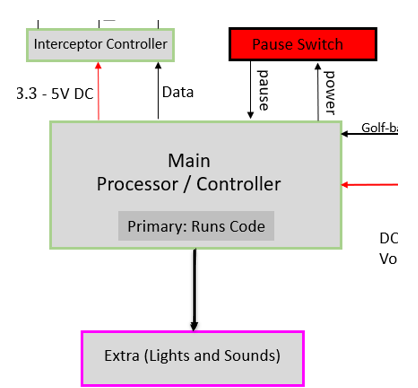
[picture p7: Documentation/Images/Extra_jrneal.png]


Figure 1: Extra subsystem and the pause switch can be seen in this figure.

- The goal of this subsystem is to implement a pause switch, make sounds before firing, and lights. The system needs a pause switch to deactivate it between rounds. This is needed to allow the judges to reset the gameboard. When the system is in the pause state the array of Red LED's will be lit up and when the system is in the run state the array of Green LED's will be lit up. This will clearly indicate the launcher's current status. The launcher is active when the LED's are Green and inactive when the LED's are Red. The buzzer will play a sound right before the launcher fires. All of the components will be implemented on a PCB.

## **Constraints:**

| **Number:** | **Constraint:** | **Origin:** | 
| --- | --- | --- |
| 1. |  The interceptor shall have a switch that sets the system into a pause state that will keep the interceptor from firing. | Rulebook |
| 2. | The voltage switched by the pause switch shall be 5V. | System Constraint|
| 3. | The interceptor must have lights that are bright enough to be seen by the judges approximately six and a half feet away, which is the longest length of the gameboard. Therefore the lights must have a candela rating greater than that of a fire alarm which is 15 cd [1]. These lights must also emit a light that falls within the visual light spectrum of 380 to 720 nanometers [2]. | Rulebook / System |
| 4. | The interceptor must make sounds before firing. The sounds will need to fall within the range of frequency humans can hear which is 20 to 20,000Hz [3]. The volume, or loudness, must be 10db above the average of the room [3], which usually falls at 60 dB [3], in order for the judges to hear the sound. The sound must also not exceed 85dB for more than eight hours or it may cause hearing damage [3]. | Rulebook / Safety |
   
1. One of the requirements in the rulebook, given to us by the customer, is that the interceptor needs to have a pause switch that keeps the interceptor from firing when the board is being reset. This switch will need to be physical, but in the implementation, it will run to the processor where it will prevent it from outputting any signals. When the switch is engaged it will keep the processor block from outputting signals to the mechanical system. This will ensure that the interceptor does not fire while the judges are in the competition area. The color red will indicate that the launcher is inactive and green will indicate that the launcher is active.
   
2. The circuit that is implemented by the pause switch needs to fall within the limitations of the processor block. Based on the processors that could be chosen the voltage that will be switched will be 5V. This source will be connected to a PCB that will be connecting the circuit components.

3. To add to the total points for the competition, the interceptor must have lights. This constraint can be found in the official rulebook for the competition. Light that falls within the spectrum that we can see, which falls within 380 to 720 nanometers [2], is sufficient. Therefore two arrays of ten LED's will be used for this. Both of these LED's fall within these parameters. The LED's must be viewable by the judges from a minimum of 6.5ft. An applicable example of lights within a building, other than the room lighting, is a fire alarm. The current ADA expected candela value is a minimum of 15cd. If this rating is official for getting the attention of hearing impared people in a room, then it will be enough light to be seen by the judges 6.5ft away. 
   
4. To add to the total points for the competition, the interceptor must make sounds before firing. This constraint can be found in the official rulebook for the competition. The piezo buzzer must be able to work with an output of the Jetson Nano which will be 5V. It must also fall within the human hearing range of frequency which is 20 to approximately 20,000Hz. The piezo buzzer that was chosen operates at a frequency of 2500Hz to 3500Hz which will fall within the frequency range that humans can hear. When it comes to loudness, humans can tolerate a range of 0 to 120db and the sound must not exceed 85db for long periods which will keep the noise at a safe level [3]. The buzzer also needs to be 10db louder than the noise in the room which is the qualification for paging speakers [2]. The average room noise is 50db, therefore the buzzer should produce a noise with a minimum loudness of 60db. 
   
## Buildable Schematic
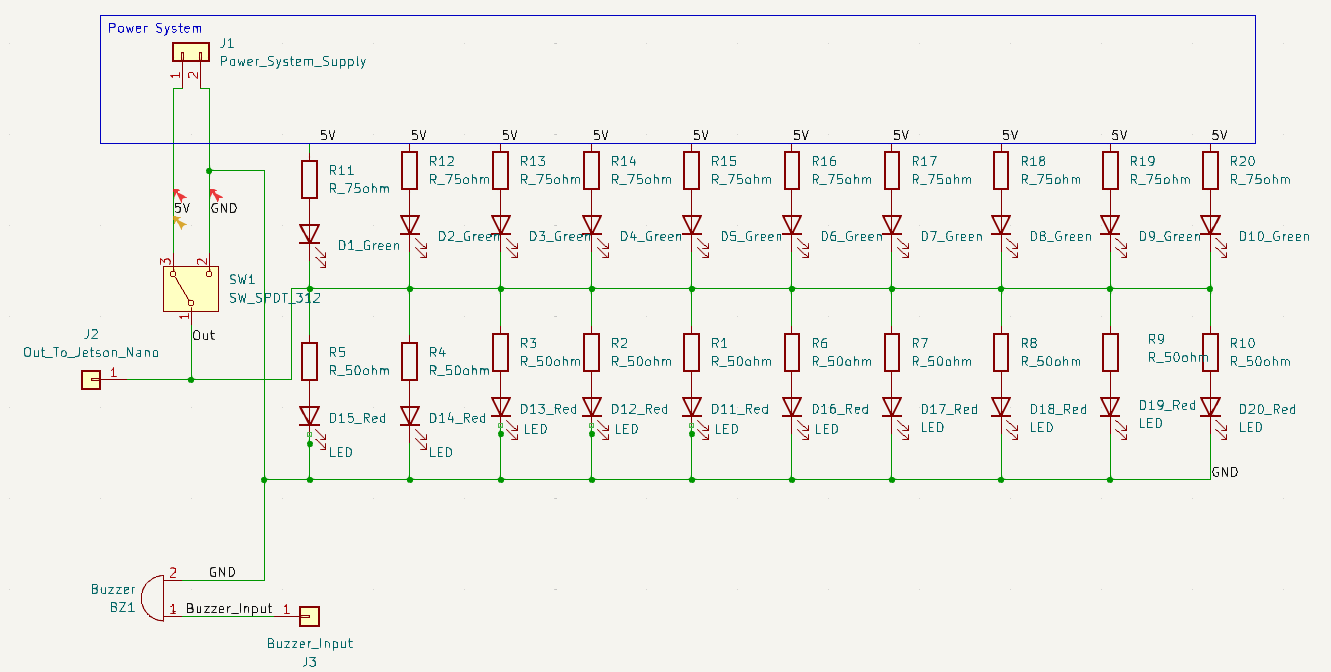
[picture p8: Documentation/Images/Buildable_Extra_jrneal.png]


Figure 1: This represents the buildable schematic for the pause switch. This switch outputs 5V or ground that comes from the power subsystem. This output is sent to the processor block to determine the pause state. In this example, the green LED's will be at the top, and the red LED's will be at the bottom. 

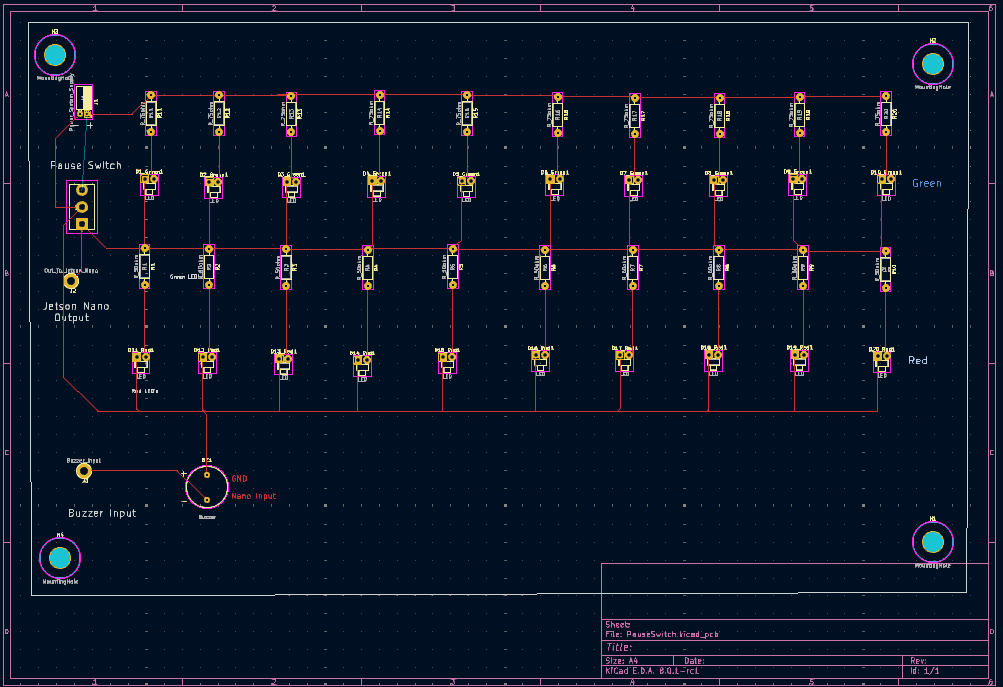
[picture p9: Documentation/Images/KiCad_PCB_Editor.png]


Figure 2: This image shows the PCB Editor view of the PCB. 

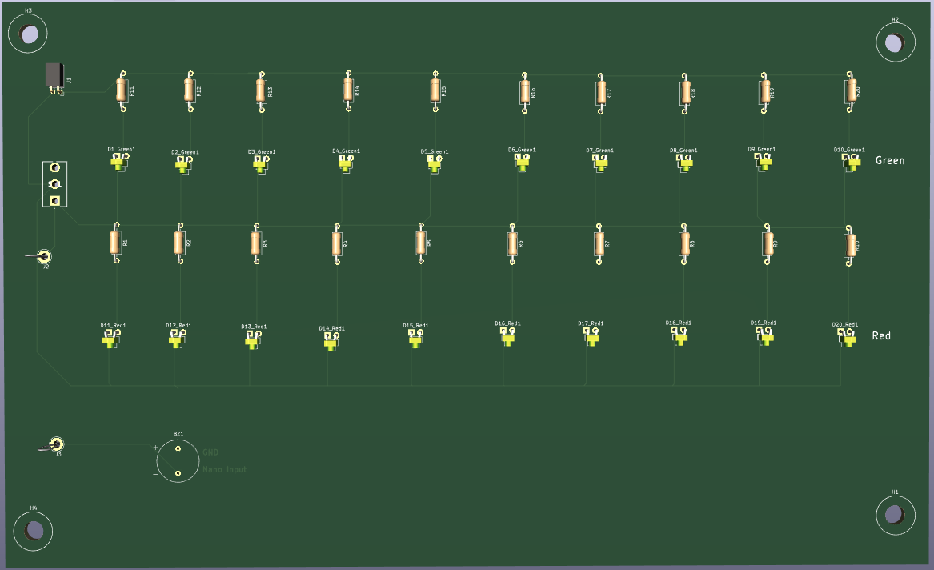
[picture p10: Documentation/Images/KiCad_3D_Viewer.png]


Figure 3: This image shows the 3D view of the PCB.

## **Analysis**
For the pause switch component, there are many different switches that can be chosen. Switches range between single pole single throw and upwards. The switch that needs to be implemented for the pause switch should be a single pole double-throw switch that has a two on functions and an off function. This will ensure that with one connection the processor will be receiving 5V, which will count as a binary one, and when the switch is off the processor will be connected to ground which will be interpreted as a binary zero. The switch that was chosen for this task is the CIT Relay and Switch, ANT11SF1CQE [5]. This switch is rated for 5A and 28VDC which will be more than enough for this simple task. The other main portion of the pause switch is the implementation in the code of the processor. The Jetson Nano has been chosen as the processor that will be recieving the data. To be clear when the pause switch is on 5V will be allowed to pass and when it is off the circuit will be connected to ground. This input will be interpreted as a variable and when the circuit is switched to ground, the processor will be allowed to collect the data from the sensors. When the switch is set to 5V the processor will be in the pause state where it can not do anything but wait for the switch to be turned off.

When the output of the switch is connected to 5V this will be sent to the processor and an array of ten red LED's [6], with a wavelength of 624nm, and ten current limiting resistors that will indicate that the interceptor has been put into pause mode. This set of LED's will be connected to the processor node on one side and the gound on the other. This will allow current to flow when the switch is connected to 5V and will show that the interceptor is in the pause state. The array of ten green LED's [7], with a wavelength of 525nm, will be connected to the processor node on one side and 5V from the power subsystem on the other. When the switch is connected to the ground current will flow from the 5V to the ground which will light up the green LED's. This will serve to show that the interceptor is ready to fire.

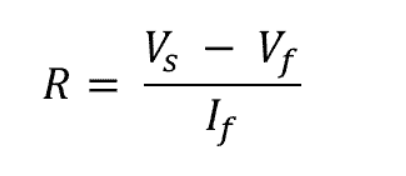
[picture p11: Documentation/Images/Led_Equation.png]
 [8]

The rated current for the LED's is 20mA for the green LED's and for the red it is 50mA. Because of the 5V being used a resistor value was chosen, using the equation above [8], to keep the LED's below their maximum ratings. Both resistors share the same Vs of 5V. The values for the red LED were found using the datasheet those values are: Vf = 2.5 (max of 3.0V) and If DC = max of 50mA [9]. For the green LED's the datasheet was used to find values of Vf = 3V (average) and If DC = 20mA max [10]. These values were then put into the equation above and resistance values were calculated to make both resistors. The green LED's need a resistance of 100 Ohm [11] and the red LED's need a resistance of 50 Ohm [12]. For the green LED this sets the voltage at 3V and the current at 20mA. This allows for the light intensity to be calculated from the datasheet, at 20mA the LED is rated for 25cd [10]. For the red LED, the values are set at 2.5V and 50mA. Based on the datasheet, a current of 50mA produces a value of 25cd [9]. This sets the power consumtion at 0.125W for the red LED and 0.03W for the green LED, according to the first equation below. For the resistors the power consumtion is 40mW for the 100 Ohm resistor and 125mW for the 50 Ohm resistor. For the 100 Ohm resistor the power rating is 0.6W and for the 50 Ohm resistor the power rating is 0.5W. The power being consumed is below the power ratings therefore the resistors will not burn up.

$$P=VI$$

The candela value for fire alarms was taken from the Americans with Disabilities Act's (ADA) guidelines on accessable designs. This value, which is considered enough light to get the attention of hearing impared individuals, has an ADA anticipated value of 15cd. This value takes into account ambient light and if the strobe is in the middle of the room [1]. Therefore, if this value is considered the standard for getting the attention of deaf individuals during an emergency, it will be adequate for viewing from approximately 6.5ft away by the judges. Just to be sure, once again the green and red LED's both have an output of 25cd which surpasses the given requirement. There is also an array of ten of them to increase the overall brightness for the judges.

The wiring schematic can be seen in figure one. The wiring diagram is very simple and only involves a few connections. The power source comes directly from the power block. The connection for the buzzer circuit would be from the GPIO (General Purpose Input Output) pins on the Jetson Nano to one connection of the buzzer and then the other connection will be connected to the ground of the board. The next connection would be the 5V terminal to the PCB and the second would be the ground. All that would be left is the code for making the sounds. The code written would need to send 5V to the piezo buzzer which would allow it to play a sound. This sound would be played for a defined period of time when the processor recieves the proper signal. This signal will most likely be the aiming signal and the sounds will be played for a predetermined amount of time. The buzzer that was chosen is the PUI Audio, Inc. AI-1223-TWT-5V-7 [15]. This buzzer is rated for 5V and is internally driven which means that no driver circuitry is needed. This buzzer needs to have a decibel value at 6.5ft that falls within the rating for paging speakers which is 10db above the ambient noise level [4]. The equation below [14] shows the relationship between decibels and distance. As distance increases the decible level drops. As the datasheet for the buzzer states, the rating for the chosen buzzer is 85db at 5V from 10cm away [13]. A calculation from 6.5ft away (1.98m) shows that the decibel level will be reduced by 25.93db, therefore the decibel rating at 6ft (1.83m) will be 85db - 25.2db which is 59.8db. This value falls right at the needed 60db which is the decibel qulifications of a paging speaker. As long as the judges are within 6ft of the buzzer they will be able to hear it over the room noise. Because the qualifications of the paging speaker are met, the judges will be able to hear the buzzer from 6ft or less (1.82m). 

$$dL =  20 log (R2 / R1) [14]$$

## Bill of Materials

| **Items:** | **Quantity:** | **Price:** | **Total:** |
| --- | --- | --- | --- |
| CIT Relay and Switch, ANT11SF1CQE (Switch) | 1 | $3.48 | $3.48 |
|  Vishay Semiconductor Opto Division, VLCS5130 (Red LED) | 10 | $4.10 | $7.58 |
|  American Bright Optoelectronics Corporation, BL-BGX3V1 (Green LED) | 10 | $3.47 | $11.05 |
|  TE Connectivity Passive Product, LR1F100R (100 Ohm Resistor) | 10 | $0.55 | $ 11.60|
|  Vishay Dale, CMF5550R000FKEK70 (50 Ohm resistor) | 10 | $3.78 | $15.38 |
|  PUI Audio, Inc. AI-1223-TWT-5V-7 (Buzzer) | 1 | $4.81 | $20.19 |

| **Item:** | **URL** |
| --- | --- |
| CIT Relay and Switch, ANT11SF1CQE (Switch) |  https://www.digikey.com/en/products/detail/cit-relay-and-switch/ANT11SF1CQE/12503396 |
| Vishay Semiconductor Opto Division, VLCS5130 (Red LED) | https://www.digikey.com/en/products/detail/vishay-semiconductor-opto-division/VLCS5130/4073547 |
| American Bright Optoelectronics Corporation, BL-BGX3V1 (Green LED) | https://www.digikey.com/en/products/detail/american-bright-optoelectronics-corporation/BL-BGX3V1/9678159 |
|  TE Connectivity Passive Product, LR1F100R (100 Ohm Resistor) | https://www.digikey.com/en/products/detail/te-connectivity-passive-product/LR1F100R/2381158 |
| Vishay Dale, CMF5550R000FKEK70 (50 Ohm Resistor) | https://www.digikey.com/en/products/detail/vishay-dale/CMF5550R000FKEK70/3616606 |
| PUI Audio, Inc. AI-1223-TWT-5V-7 (Buzzer) | https://www.digikey.com/en/products/detail/pui-audio-inc/AI-1223-TWT-5V-7/21689820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 |

## References
1. “Audible/Visible Appliance Reference Guide Introduction: The Need for an Audible/Visible Compliance Reference Guide.”, firetechs.net, https://www.firetechs.net/library/ReferenceGuides/SystemSensor/AudibleVisibleRefGuide.pdf (accessed Apr. 22, 2024).
2.  A. Hadhazy, “What are the limits of human vision?,” BBC News, https://www.bbc.com/future/article/20150727-what-are-the-limits-of-human-vision (accessed Apr. 17, 2024).
3. “What is the human hearing range in hz and DB?: Miracle-ear,” Miracle Ear, https://www.miracle-ear.com/blog-news/human-hearing-range (accessed Apr. 17, 2024).
4. B. Mesnik, “What is the right sound level for your paging speakers?,” Kintronics, https://kintronics.com/right-sound-level-paging-system/ (accessed Apr. 23, 2024). 
5. “Ant11sf1cqe CIT relay and switch | switches | DigiKey,” Digikey, https://www.digikey.com/en/products/detail/cit-relay-and-switch/ANT11SF1CQE/12503396 (accessed Apr. 16, 2024). 
6. “VLCS5130,” DigiKey, https://www.digikey.com/en/products/detail/vishay-semiconductor-opto-division/VLCS5130/4073547 (accessed Apr. 21, 2024).
7. “BL-BGX3V1,” DigiKey, https://www.digikey.com/en/products/detail/american-bright-optoelectronics-corporation/BL-BGX3V1/9678159 (accessed Apr. 21, 2024). 
8. V. Lynch, “Led resistor calculator,” The Engineering Mindset, https://theengineeringmindset.com/led-resistor-calculator/ (accessed Apr. 21, 2024). 
9. “VLCS5130,” Vishay, https://www.vishay.com/docs/81938/vlcs5130.pdf (accessed Apr. 21, 2024). 
10. “BL-BGX3V1,” BRIGHT LED ElLECTRONICS CORP., https://www.americanbrightled.com/pdffiles/led-components/through-hole/BL-BGX3V1.pdf (accessed Apr. 21, 2024). 
11. “LR1F100R,” DigiKey, https://www.digikey.com/en/products/detail/te-connectivity-passive-product/LR1F100R/2381158 (accessed Apr. 28, 2024). 
12. “CMF5550R000FKEK70,” DigiKey, https://www.digikey.com/en/products/detail/vishay-dale/CMF5550R000FKEK70/3616606 (accessed Apr. 21, 2024). 
13. “AI-1223-TWT-5V-7,” DigiKey, https://www.digikey.com/en/products/detail/pui-audio-inc/AI-1223-TWT-5V-7/21689820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 (accessed Aug. 27, 2024).  
14. E. Engineeringtoolbox, “Sound propagation - The Inverse Square Law,” Engineering ToolBox, https://www.engineeringtoolbox.com/inverse-square-law-d_890.html (accessed Apr. 23, 2024). 

‌

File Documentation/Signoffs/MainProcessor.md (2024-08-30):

# **Function:**

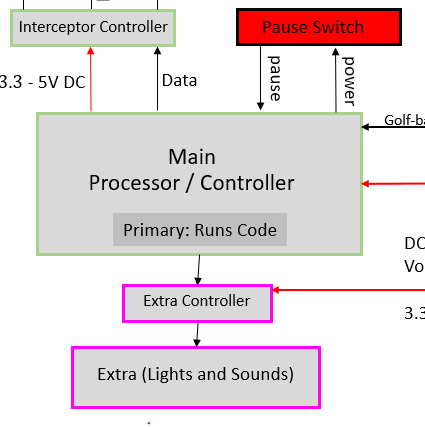
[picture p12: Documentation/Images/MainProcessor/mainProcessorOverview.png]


*Figure 1: Main Processor Overview*

The main processor unit is responsible for receiving, analyzing, and interpreting data from the image-detecting system to calculate and aim the interceptor. Its primary function revolves around processing data related to a golf ball's trajectory in real time. The Jetson Nano serves as the brain of the system, consolidating data from the local camera that passes the data to the main processor.

## **Constraints:**

| NO. |	Constraint | Origin |
|-----|---|---|
| 1	| Time Constraints - Real-time data processing for trajectory prediction for the golf ball can not take longer than the total time for each image. The main processor needs to calculate the ball data before the ball reaches the end which varies from 1.9 seconds to 7.4 seconds | System Constraint |
| 2	| Processing Speed - The main processor scripts and programs have to be optimized for efficient calculations. The scripts get the speed, wire, and variable height from input data. These calculations should not take longer than their required time per calculation iteration | System Constraint |
| 3	| Resource Utilization - Since the board has 1.43GHz with quad-cores and 4GB RAM, the main processor needs to be utilized properly to prevent an overload of system resources. The system needs to use all cores and not overload the RAM for speed efficiency but not sacrifice stability | System Constraint |
| 4 | Pausing Processes: The system needs a pause state to stop other scripts from activating firing mechanisms. | Rulebook |

## **Fulfilling Constraints:**

**Time Constraints:** The Jetson Nano has a worst-case scenario of 1.9 seconds to find the golf ball and calculate and aim the interceptor's position before the ball reaches the end, given by Devcom. Real-time processing of sensor data and trajectory calculations impose time constraints on the Jetson Nano. Since it has to be able to detect and calculate the proper position of the ball. Its 1.43GHz quad-core ARM Cortex-A57 processor needs to be able to receive, process, calculate the interceptor’s path, and aim the interceptor before the golf ball gets too far down the string [3]. The ball's travel time varies from 1.9 seconds to 7.4 seconds and the programs and data transmission needs to be optimized for an accurate and efficient system to be able to run fast enough. Delays in data acquisition, processing, or interceptor firing may affect the interception accuracy dramatically [2].

**Processing Speed:** The data gathered and calculated from the image processing is the worst case of 357.42ms from the image processing subsystem. The Jetson Nano needs to calculate and simultaneously send data to the firing mechanism Arduino. These tasks may strain the processing capabilities of the Jetson Nano, potentially leading to performance bottlenecks. The algorithms need to utilize the hardware and run scripts on multi-core to limit any speed limitations. Based on benchmarks used in image processing to find the position of the goldball will take 1.8ms for the moment calculations and 10ms for the centroid calculation [10]. This will give the X, and Y coordinates of the center of the goofball--giving the position of the golfball. The assumption for comparison is linear time for 10ms making the total for each image 21.8ms. Since three images will be used to extract all the data, the final time will be 65.4ms for all three images.

**Resource Utilization:** With a limited 4GB of LPDDR4 RAM, the Jetson Nano needs to use the resources but with image processing, it could easily have a resource overload. The memory and CPU load cannot be overloaded or the system's responsiveness will hinder its operation [2].

**Pausing Processes:** The rulebook from Devcom states the requirement for a pause switch integrated with the interceptor to stop the machine from firing. The constraint is pausing the script or scripts from running and operating as it is intended when the switch is on [9].

# **Buildable Schematic:**
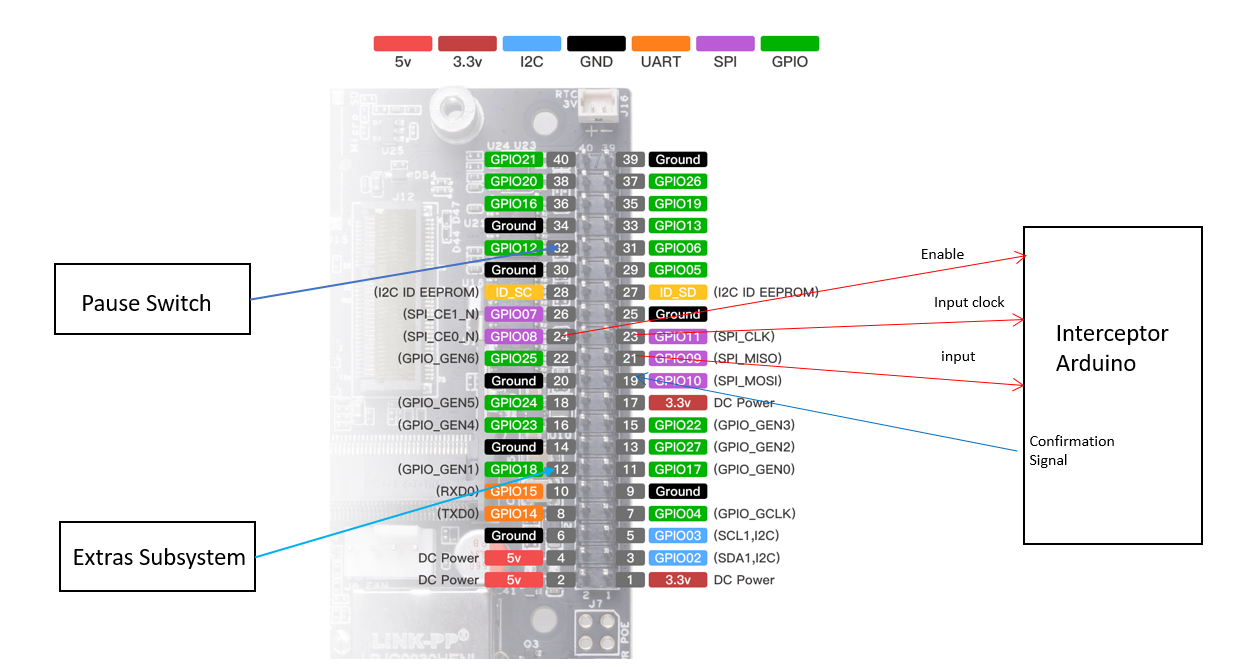
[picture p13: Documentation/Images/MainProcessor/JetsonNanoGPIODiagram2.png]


*Figure 2: Jetson Nano Wiring Schematic*

## **Analysis of Using Jetson Nano:**

Python remains the primary programming language for interfacing with the Jetson Nano due to its versatility and extensive libraries. Additionally, C++ may be employed for computationally intensive tasks, leveraging the Jetson Nano's GPU for accelerated computations. [5]

**Hardware Configuration:** The Jetson Nano interfaces with the other hardware components with the GPIO pins. GPIO pins such as GPIO05, GPIO06, GPIO13, GPIO12, and GPIO18 facilitate flexible input/output operations, accommodating sensor connections and interceptor control. While using GPIO02 and GPIO03 for the SCL and SDA data [3].

**Programs and Tasks:** Custom Python scripts control various system tasks, including signal processing, trajectory calculations, and interceptor control. Multithreading may be applied to enable concurrent execution of tasks, maximizing system efficiency.

**Data Processing and Calculations:** Upon receiving the image detection data, the Jetson Nano executes trajectory calculations to determine the golf ball's velocity, height, distance, and direction. Mathematical algorithms will be used to accurately determine the data.

The height calculations will need the height of the camera, the image height of the bounding box in pixels, and the physical height of the two possible positions [1]. The given information from the image processing will be the given X-Axis and Y-Axis that will be used to determine the object height. Since the ball ranges from 43 inches to 50 inches in height, the system can figure out the wire the ball is on and the height the ball will be on.
~~~math
Object Height = ( Physical Height * Y-Axis )/( Image Height ) + Ball Offset
~~~
Test data from input from image processing axis data:
~~~math
Object Height = (4 inches * 730 pixels ) / ( 1080 pixels) + 42 inches
~~~
~~~math
= (2,920 pixel inches)/(1080 pixels) + 42 inches = 44.7 inches
~~~

The Speed calculations will be taking the distance or position of the object over time [1]. The frames of the objects location can calculate the speed using the following equation. The speed calculations will be determined using different distances and time frames sent from the image detection to determine how fast the ball is traveling. There will be 119.17ms between each retrieval of position, which will allow the calculation of speed. While using backlogged data of testing speeds, the system will also figure out speeds and compare to increase the overall accuracy of the speed [1].
~~~math
Speed = (DistanceOne - DistanceTwo) / Change in Time Between Frames
~~~

Test data from input from image processing distance data:
~~~math
Speed = (53 inches - 48 inches) / (0.1692 seconds)
~~~
~~~math
= (5 inches)/(0.1692 seconds) = 29.55 inches/second
~~~

**Control of Golf Ball Interceptor Shooter:** Based on the calculated trajectory data, the Jetson Nano will control the timing and activation of the golf ball interceptor shooting mechanism. It needs to have the interceptor to be properly aligned towards the golf ball's predicted path, and fire at the appropriate time to hit the ball mid-air. The Jetson Nano will send all the required data of the x-axis, y-axis, and firing signals to the arduino controlling the interceptor. This could use preset fire positions to optimize the interception process [6,7].

## **Analysis of Board Component Integration:**

**Pause Switch Analysis**

When the switch gives a positive 5 Volts to the Jetson Nano, we need to stop scripts from enabling the interceptor firing mechanism to halt any inappropriate firing. This adds a safety measure that the rulebook was requesting [9].

**Arduino Integration**

The Jetson Nano will integrate with the interceptor's Arduino controller aiming mechanism [7]. The Jetson Nano will communicate with the Arduino using SPI interface. The pins: 'spi_ce0_n' (Enable), 'spi_clk' (Clock), 'spi_mosi' (Master Out Slave In), and 'spi_miso' (Master In Slave Out) the pins will handle data transmission from the Jetson Nano to the Arduino and vice versa. By connecting these pins, the Jetson Nano can act as an SPI master, sending location information and firing information while receiving data from the Arduino acting as a slave.

Real-time trajectory data calculated by the Jetson Nano will then wait for the Arduino to send back a confirmation signal to confirm the position of the interceptor. This can apply to the X-Axis and Y-Axis of the system to be able to know if the interceptor controller aimed to the correct position [6].

A second Arduino will control all the extras will send signals when aiming, and possibly firing signals for the extra subsystem that controls the sounds and lights.

## **BOM:**
| Name | Description | Used in which subsystem(s) | Part Number | Manufacturer | Quantity |	Price |	Total |
|---|---|---|---|---|---|---|---|
|Jetson Nano Developer Kit | This component is meant to process incoming data and find the aiming position and firing time for the interceptor | Main Processor, Image Processing | 945-13450-0000-000 | NVIDIA | 	1 |	$229.38|	$229.38 |
| Total | | | | | | | 			$229.38|

The Jetson Nano offers an affordable yet powerful solution for system control, priced at $229.38 [4]. This ensures cost-effectiveness without compromising performance for doing image processing calculations.

## **References:**

[1] N. shukla, “A review on image based target distance & height ...,” Research Publish, https://www.researchpublish.com/upload/book/A Review on Image Based Target Distance-1172.pdf (accessed Apr. 11, 2024). 

[2] “NVIDIA® Jetson Nano 4GB development kit,” OKdo, https://www.okdo.com/us/p/nvidia-jetson-nano-4gb-development-kit/ (accessed Apr. 11, 2024).

[3] “Jetson nano developer kit by Nvidia: 945-13450-0000-000,” Arrow.com, https://www.arrow.com/en/products/945-13450-0000-000/nvidia (accessed Apr. 11, 2024).

[4] Walmart, https://www.walmart.com/ip/NVIDIA-Jetson-Nano-Developer-Kit/480691437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 (accessed Apr. 11, 2024).

[5] Dr. M. Nazeer, M. Qayyum, and A. Ahad, “Real time object detection and recognition in machine learning using Jetson Nano,” SSRN, https://papers.ssrn.com/sol3/papers.cfm?abstract_id=4286087 (accessed Apr. 11, 2024). 

[6] “Five steps to connect Jetson Nano and Arduino,” Rareschool, https://blog.rareschool.com/2019/05/five-steps-to-connect-jetson-nano-and.html (accessed Apr. 17, 2024).

[7] “Connecting Jetson Nano to Arduino Uno,” NVIDIA, https://forums.developer.nvidia.com/t/connecting-jetson-nano-to-arduino-uno/172775 (accessed Apr. 17, 2024).

[8] “Toggle switches,” NTE Electronics, https://www.nteinc.com/switches/pdf/toggle-std.pdf (accessed Apr. 6, 2024).

[9] S. Hall, Devcom. Devcom, 2024. S31 Paper Wad Interceptor Challenge 2024, Rulebook, (accessed Apr. 8, 2024).

[10] K. Bapat, “Find center of a Blob (centroid) using opencv (c++/python),” LearnOpenCV, https://learnopencv.com/find-center-of-blob-centroid-using-opencv-cpp-python/ (accessed Aug. 27, 2024).

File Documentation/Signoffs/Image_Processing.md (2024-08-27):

# Image Processing Subsystem

**Function:**

The goal of this subsystem is to receive and process the data from the camera sensor to determine the position and speed of the practice golf ball.  

**Constraints:**

| NO. | Constraint | Origin |
|-----|---|---|
| 1| Must be able to distinguish the golf ball from surroundings based on golf ball's shape and color | System Requirement|
| 2| Must be able to extract the x,y coordinates of the golf ball with an inch of accuracy to distinguish between the wires and variable height| System Requirement|
| 3| Must be able to receive the data and perform calculations in 500 ms to allow the interceptor time to aim and shoot based on the calculations| System Requirement|

1. In order for the system to properly detect the golf ball and extract the necessary information for aiming, the system needs to distinguish the golf ball
   from the rest of the image. Then, edge and contour detection techniques will be used to find the golf ball based on it's round shape.
2. The position of the wires are four inches apart from six feet away. Because of this, the error cannot be two inches because if it is in between two
   wires, there is no way to know if it is two inches to the right or left. However, if the error is one inch to the right or left of a wire, it will still
   be closest to the wire it is on. All pixels need to have the same error. Since the two heights are seven inches apart, the wire positions are the
   constricting factor. The ball has to be detected as soon as it is released for the interceptor to have enough time to launch the projectile. Thus, one
   inch of error is allowed for the detection of the golf ball. 
3. The fastest speed of the golf ball is 1.95 seconds based on empirical data from the customer. The ball needs to be detected in enough time for the
   launcher to aim and launch the projectile. This minimum allows time for the motors to make adjustments and fire after the information has been received
   and interpreted which is expected to take half a second each. The 500 ms will be split between the image processing and calculations for position,
   speed, and acceleration.

**Buildable Schematic**

The system is purely software. Any connections for the processor should be shown in that subsystems schematic.

A flow chart of the code is given below.

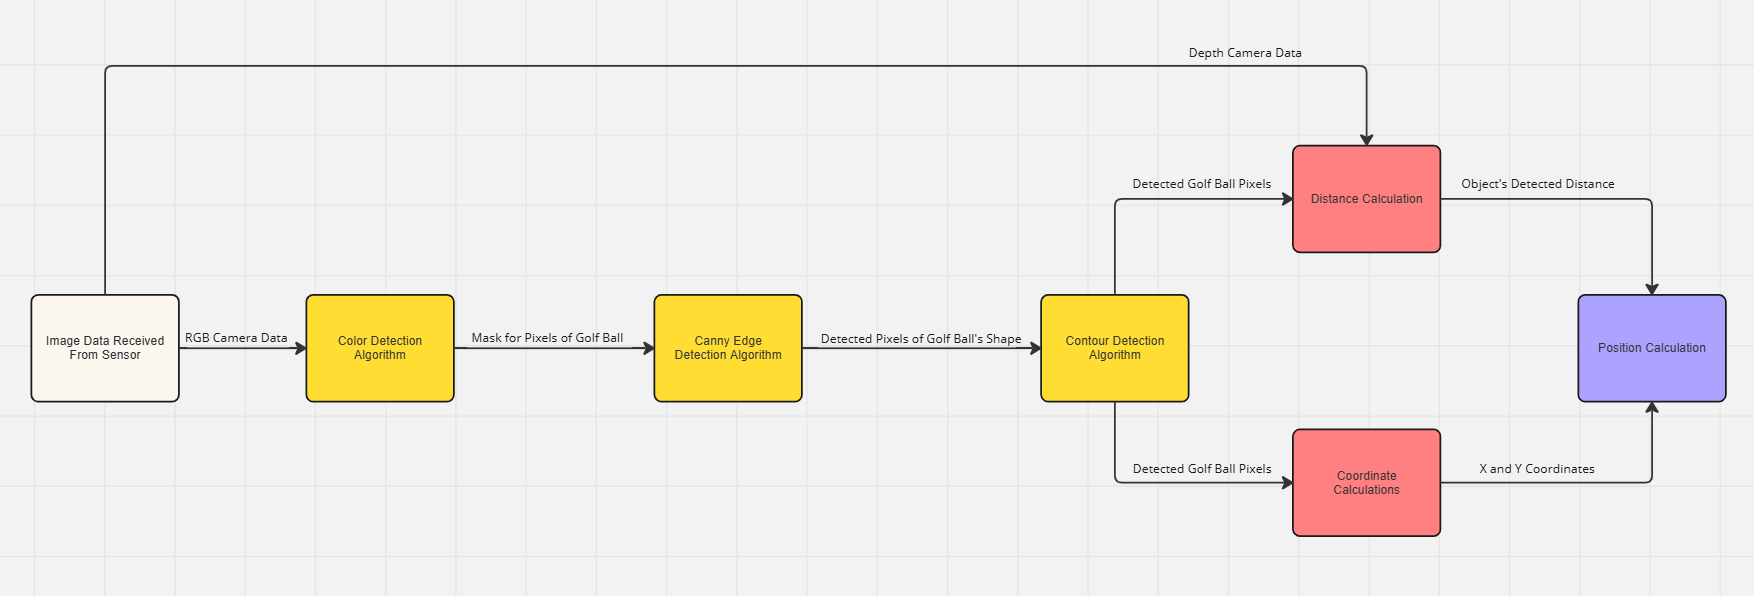
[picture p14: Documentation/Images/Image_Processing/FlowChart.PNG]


This shows the steps for each major calculation and what is necessary for each calculation. This process will be done twice to receive two positions for the
speed calculation done by the processor.

**Analysis:**

*Detection*

The golf ball will have a unique color and shape combination that will allow the object to be detected. Using color since the white golf ball can be
distinguished from other white objects while keeping its shape intact. This can be done using hue, saturation, and variation color detection. The 
boundaries for the color are determined and entered in as limits for each of these values. These parameters and the image are then sent to a function 
called inRange. This will apply a mask to the array of pixels representing the image with a mask to determine the objects with the color. The results of 
such operations and algorithms can be seen below to detect a light color like grey.

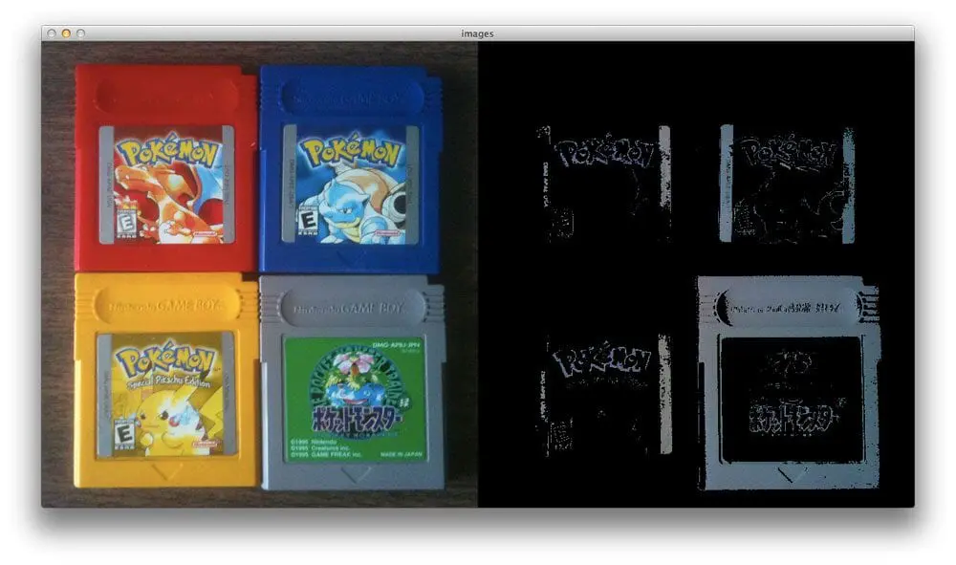
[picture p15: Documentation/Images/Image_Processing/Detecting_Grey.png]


This can be adjusted to detect a white ball by adjusting the saturation parameters for the color detection. The algorithm's parameters for the
intensity of the color can also be adjusted. The Big O analysis of this function would be O(n) because it is an iterative function that will go through all
of the pixels provided [1].

Once the golf ball has been detected based on color, the pixels representing the color can have an edge detection algorithm applied to it. With the
contrast from the added lighting that will be implemented, the features of the golf ball will be distinct from any other pixels not representing the golf
ball in the color detection results, similar to how the grey triangle on the game cartridge is still distinguishable in the picture above. The canny edge
detection would be best suited for this since it not only filters our non-edges but also sets edges as weak and strong. The golf ball will have very
strong, round edges making it highly detectable by the algorithm. The adjustable ranges to define an edge used by the open sources cv function also make it
ideal. The results of calibrated canny edge algorithms can be seen below [2].

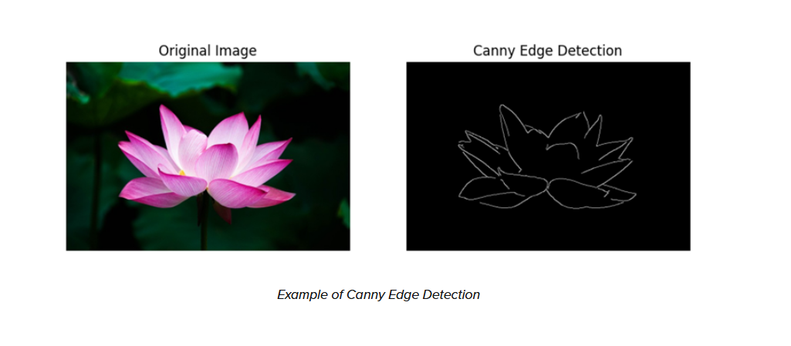
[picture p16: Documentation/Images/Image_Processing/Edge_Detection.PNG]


The Big O analysis of this function would also be O(n) since it is an iterative function through the pixels to determine if it has the qualities of an
edge. This function is most effective when the image has been cleaned and processed which is another O(n) analysis.

The exact accuracy depends on the characteristics of the golf ball and how they are picked up by the camera as well as the environment the golf ball is in.
The parameters of both these algorithms can be precisely calibrated for the given object as seen in the images from other people’s experiments and several
simulation tools available. Using these tools, I was able to simulate finding small, round objects in a picture. The results can be seen below.

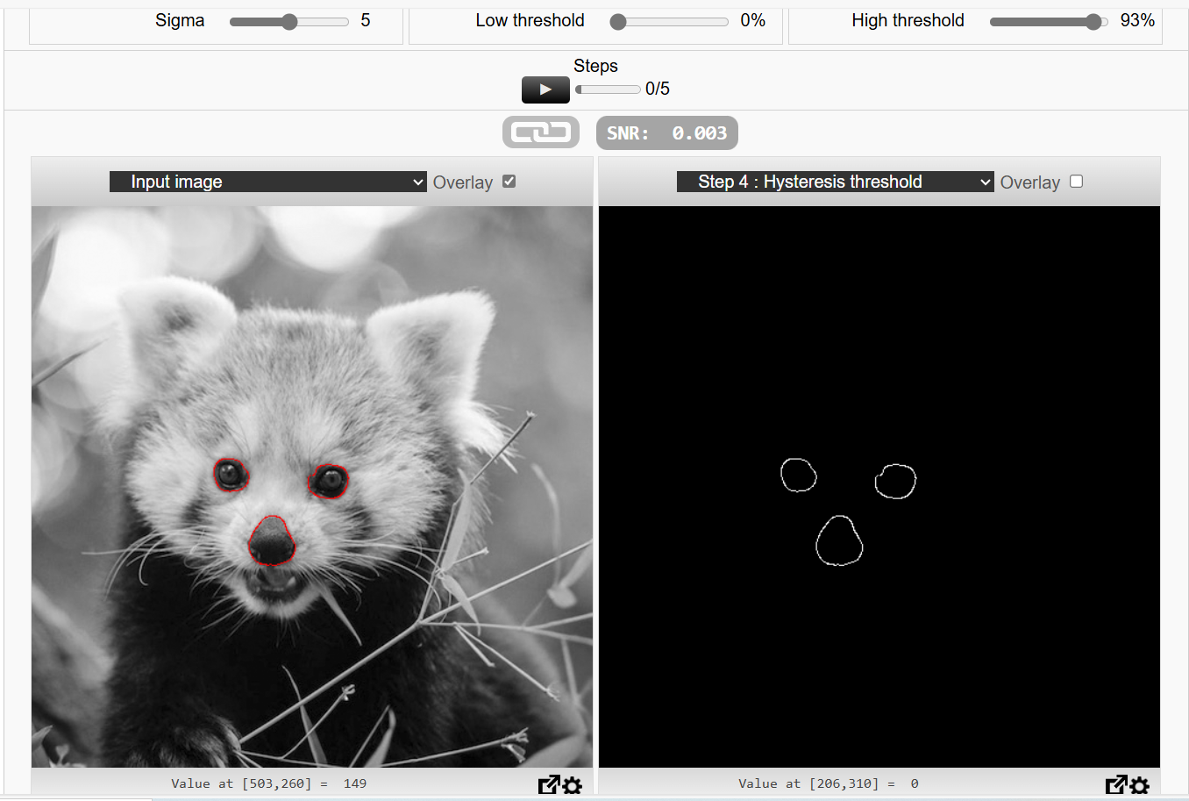
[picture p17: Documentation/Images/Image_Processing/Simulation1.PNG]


Results of altering the thresholds for detection can be seen below for finding more perfectly round objects which can be seen below.

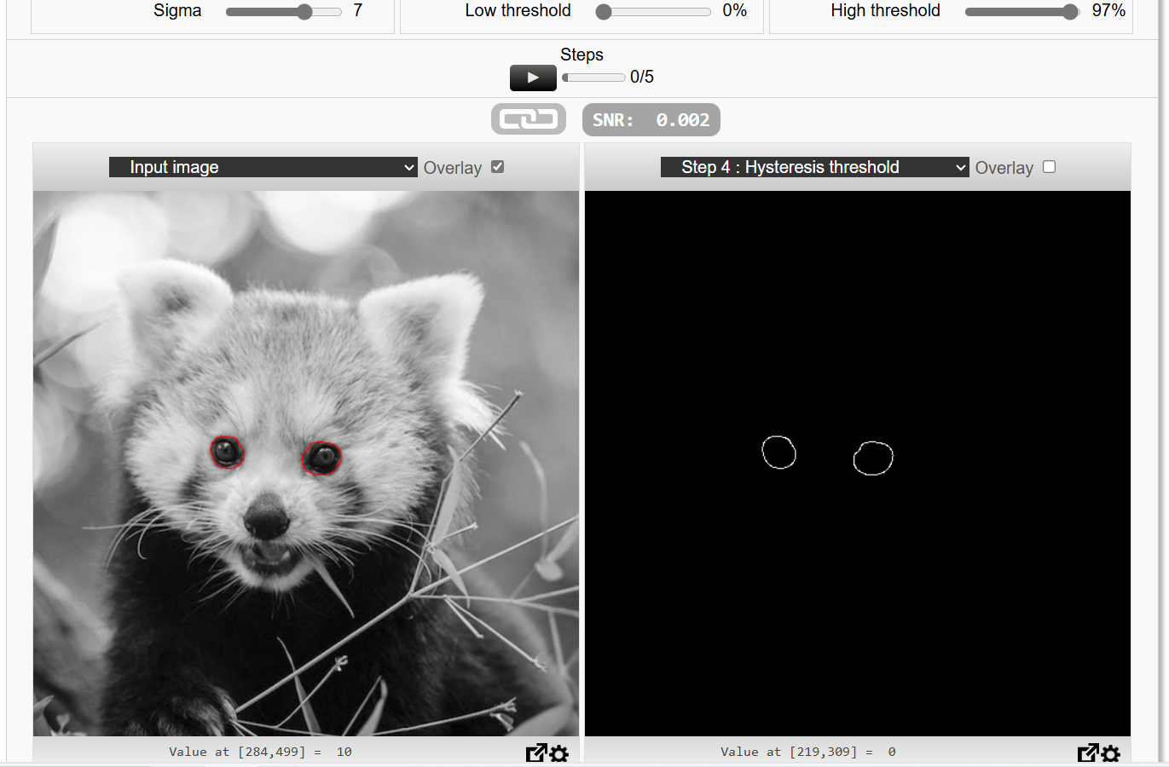
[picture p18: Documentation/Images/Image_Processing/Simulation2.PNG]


Finally, the thresholds can even be altered to distinguish between slight differences in the exact edges and contours of the image which can be seen below
[3].

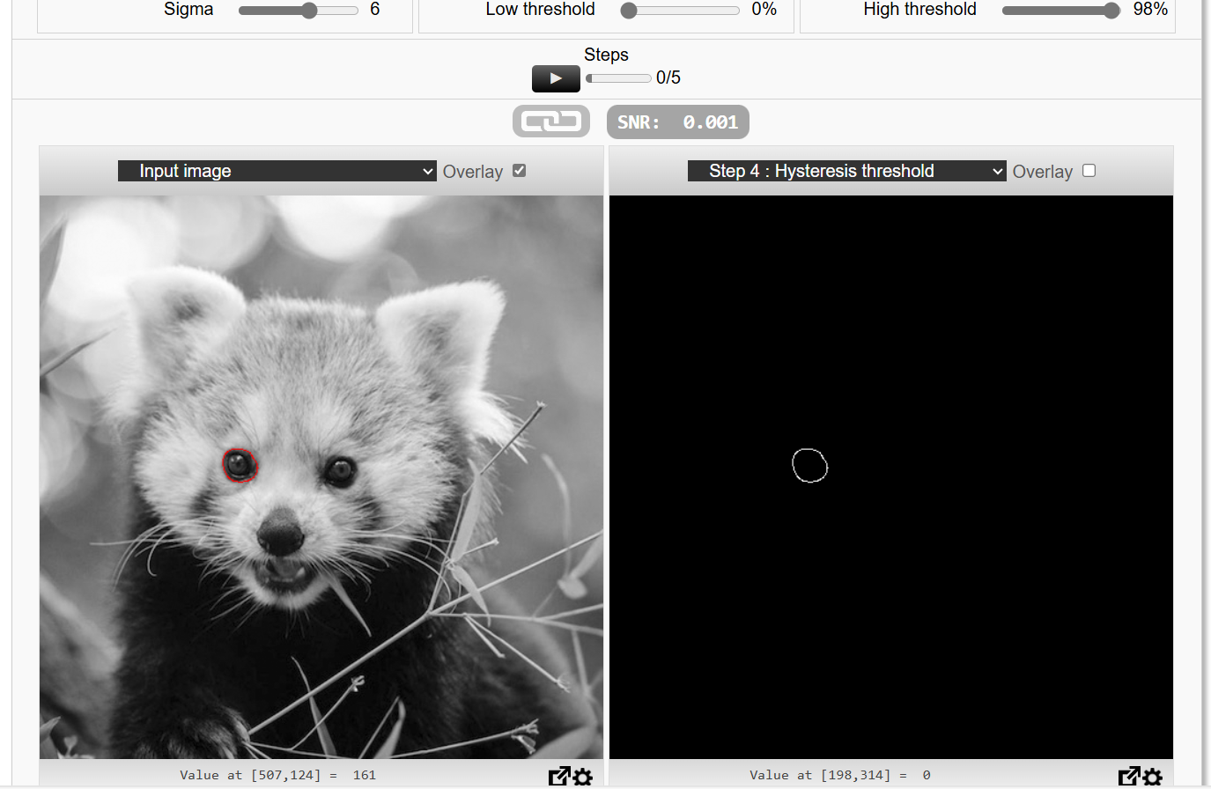
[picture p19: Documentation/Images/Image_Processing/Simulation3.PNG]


Because of this accuracy with thresholds and parameters and the preserved shapes from color detection, the golf ball should be able to be detected and
recognized by the camera via these image processing techniques.

*Distance and Coordinates*

The distance of the object can be found using another iterative function for another linear algorithm. The camera returns an array with the depth of each 
pixel. This array is compared with the array holding the pixels that represent the golf ball. The result is the depth of each pixel of the golf ball.

The object's coordinates can be determined through comparisons. Each pixel will appear to be a certain width and height. The results of the detection 
algorithm can be used to only determine the dimensions of each pixel of the object. The pixel width and height representation can be found with the 
following equations:

FOV width = 2 * tan(FOV/2) * distance and FOV height = 2 * tan(FOV/2) * distance

width per pixel = FOV width/horizontal resolution and height per pixel = FOV height/vertical resolution

The distance determination will be used to fill in the distance variable in the equation. For the distance of six feet the result will be

FOV width = 2 * tan(69/2) * 6 = 8.25 feet and FOV height = 2 * tan(42/2) * 6 = 4.61 feet

width per pixel = 8.25/1920 = 0.004296 feet/pixel * 12 = 0.05155 inches/pixel

height per pixel = 4.61/1080 * 12 = 0.004265 feet/pixel = 0.05118 inches/pixel

The amount of inches for the width and height represented by the pixels can be used to find out the x and y coordinates by multiplying the pixels by the
numbers provided [4 & 5]. The x and y coordinates can then be found by determining the pixel's coordinate in the image based on the array value of the
pixel from the original image. Then, use the calculated pixel representation to multiple the image coordinate with the real world representation. This 
should provide the real world x and y coordinates of the object. At six feet, the golf ball will only be represented by 36 pixels. Six feet is the maximum
distance the golf ball will be from the camera, so the one inch of error will be achievable. There is a 19 pixel buffer for motion blur and pixels blurring
together. Using the standard margin of error equation in statistics 

ME = Z * σ/square root of n 

where Z is the typical confidence interval of 1.96, σ is the highest filter value for the algorithm, which has been set in simulations as 10, and n is the
number of frames which will be one. Plugging these values in gives this result

ME = 1.96 * 10/1 = 19.6 pixels 

for the pixel measurements this is

0.05118 * 19.6 = 1.00 inches for the height and 0.05155 * 19.6 = 1.01 inches for the width

Lower sigma values also detect smaller objects more accurately, so the actual error is expected to be much lower. This combined with taking all the pixel
locations and averaging them together will provide a one inch accuracy for the golf ball's position. These calculations are basic arithmetic and should be
O(1). Counting the pixels is another O(n) operation, but the n number of pixels is significantly smaller due to the altered array from detecting the object.

*Speed*

The camera that is being used is 1920 by 1080 pixels. Benchmarks for the Jetson Nano Developer Kit show that for a 1920 by 1080 pixel image can resize
images in 10 ms [7]. 

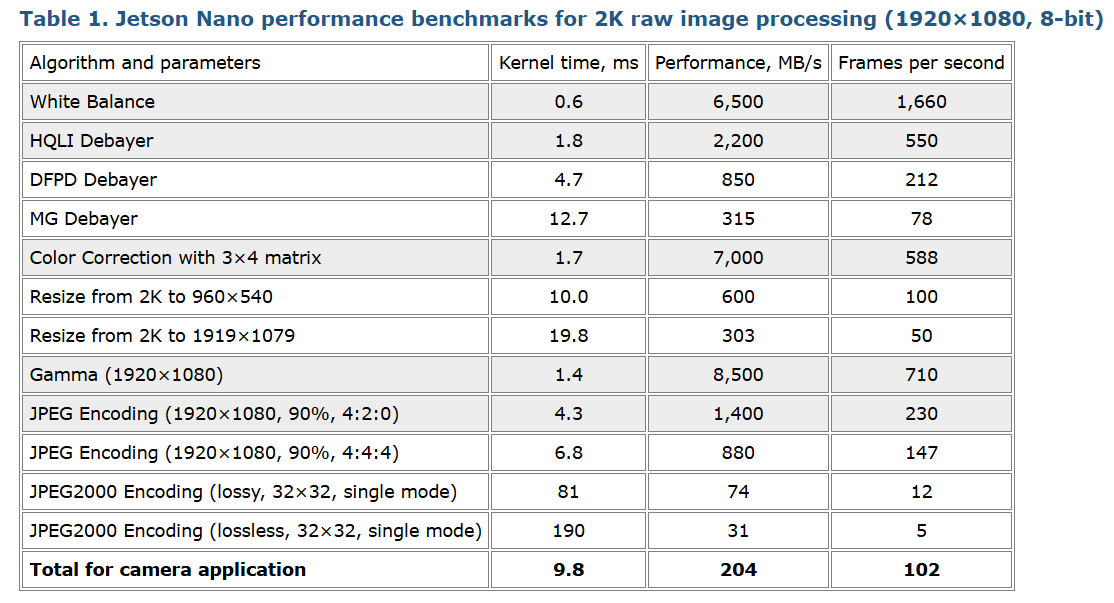
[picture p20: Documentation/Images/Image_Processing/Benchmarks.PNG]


This is an iterative process with O(n) time so it can be assumed other iterative processes with similar computation complexities will
have the same runtime. The function for color detections, applying Gaussain blur, assigning an edge value to each pixel, and finding the contours are all
iterative. The computations needed for each of this functions are also pretty similar to each other and the resize algorithm used in the benchmarks above.
The higher resolution resize is more computationally intensive, so it's runtime will be used. Each will run for 19.8 ms for a total of 79.2 ms to detect
the golf ball. The camera takes in 30 frames per second so it takes 33.33 ms to get a new image. The USB cord connecting the processor and camera processes
data at 5 Gbs. Each pixel is 8 bits and has 2 color representation bytes so the total is 

8 * 2 * 1080 * 1920 = 0.03318 Gb. 

Taking the amount of data over the rate of transfer gives 

0.03318 Gb/5 Gbs = 6.64 ms. 

The arithmetic processes for determining acceleration, speed, and other calculations to send to the launcher are considered to have O(1). This means the
most limiting time factor is how long it takes to get three positions. 

33.33 ms + 6.64 ms + 79.2 ms + 33.33 ms + 6.64 ms + 79.2 ms + 33.33 ms + 6.64 ms + 79.2 ms = 357.42 ms. 

This time period is well within the almost 1/8 time of the ball's travel given for the data to be collected and processed for the aiming and launching. It
gives nearly 7/8 of the remaining time to determine the speed and location of the ball which will then be used to aim and intercept the ball. After the
estimated 500 ms to process the image and calculate the speed and half a second each to aim and launch, 400 ms is left for the projectile to travel and
intercept the golf ball before it hits the interceptor.

**Bill of Materials:**

This subsystem is implemented as part of the processor. All camera and lighting information is part of the sensor. No additional parts needed.

**References:**

[1] A. Rosebrock, “OpenCV and python color detection,” PyImageSearch, https://pyimagesearch.com/2014/08/04/opencv-python-color-detection/ 
(accessed Apr. 15, 2024). 

[2] C. Writer, “Edge detection in image processing: An introduction,” Roboflow Blog, https://blog.roboflow.com/edge-detection/ (accessed Jun. 29, 2024). 

[3] “Big | image processing online demonstration | canny edge detector,” Image Web Demonstrations, https://bigwww.epfl.ch/demo/ip/demos/edgeDetector/ (accessed Jul. 14, 2024). 

[4] R. Awati, “What is field of view (FOV)?,” WhatIs, https://www.techtarget.com/whatis/definition/field-of-view-FOV (accessed Apr. 20, 2024). 

[5] “Understanding image quality on the MV32,” Cisco Meraki Documentation,
https://documentation.meraki.com/MV/Viewing_Video/Understanding_Image_Quality_on_the_MV32 (accessed Apr. 20, 2024). 

[6] “How to measure pixel size for image processing? | Researchgate,” ResearchGate,
https://www.researchgate.net/post/How_to_measure_pixel_size_for_image_processing (accessed Apr. 20, 2024). 

[7] F. Serzhenko, “✅ Jetson nano benchmarks for image processing,” fastcompression.com - GPU Image Processing Software,
https://www.fastcompression.com/blog/jetson-nano-benchmarks-image-processing.htm (accessed Apr. 15, 2024).

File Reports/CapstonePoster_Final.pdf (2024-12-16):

# DEVCOM Golf Ball Interceptor

Garrett Armstrong, Savannah Metzler, Jonathan Neal, Finlay Patoto, Katie Swinea, Kevin Ulrich
Tennessee Technological University

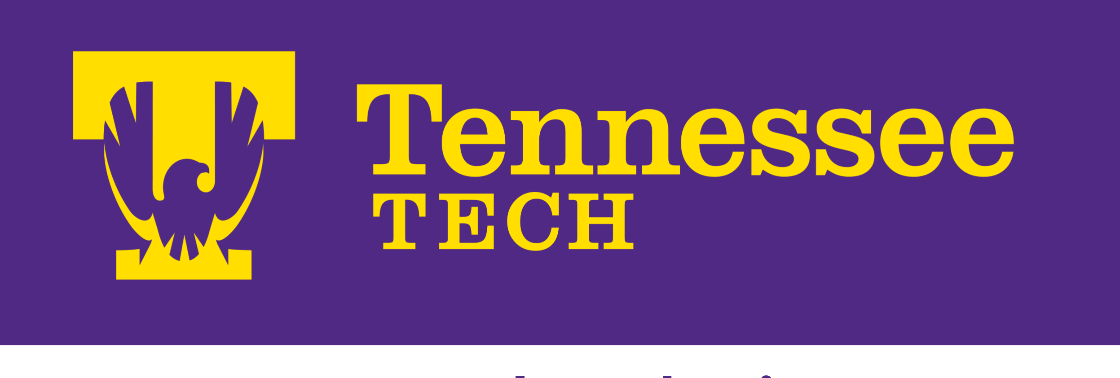
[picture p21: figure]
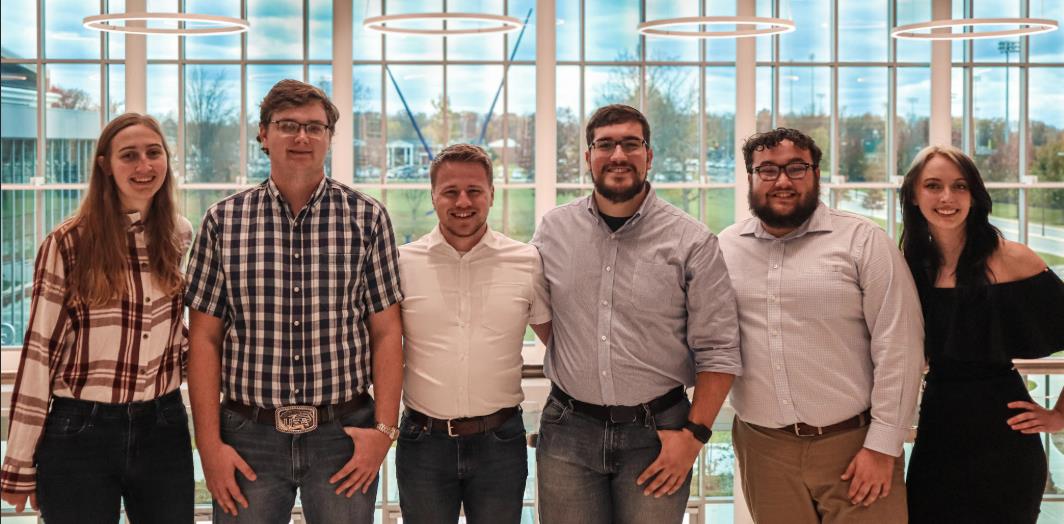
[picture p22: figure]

## Introduction

Problem: This project aims to spark student’s interest in STEM fields by replicating a missile defense system.

Constraints: The launcher must adhere to DEVCOM’s rules. For example: the launcher must fit in a 1ft-by-1ft-by-1ft box, it must not shoot further than 6ft, it must include an E-stop and pause switch, and it must function on its own during the competition.

## Design

Figure 1 below shows the completed launcher. The main components that can be seen, such as the launcher itself and housing, were made by the Mechanical Team. The insides, illuminated by the red light, are the electrical team’s contributions which are further elaborated upon below. The final projectile used can also be seen in figure two. Power: Power was split into two parts, the 24V 600W supply and a 5V 50W supply. The 24V supply powers the mechanical portion’s motors. The 5V supply powers the Processor, Motor Controller, and Extra Subsystem.

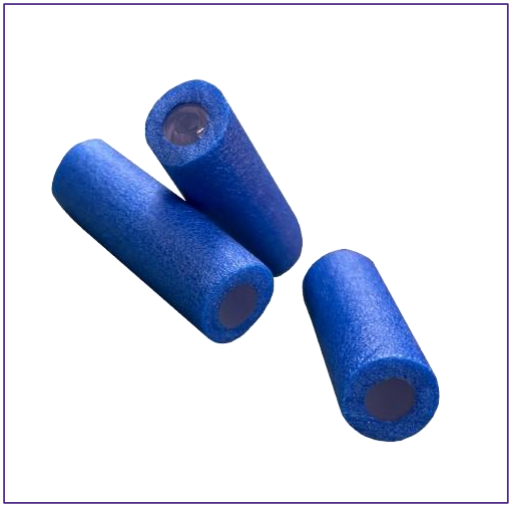
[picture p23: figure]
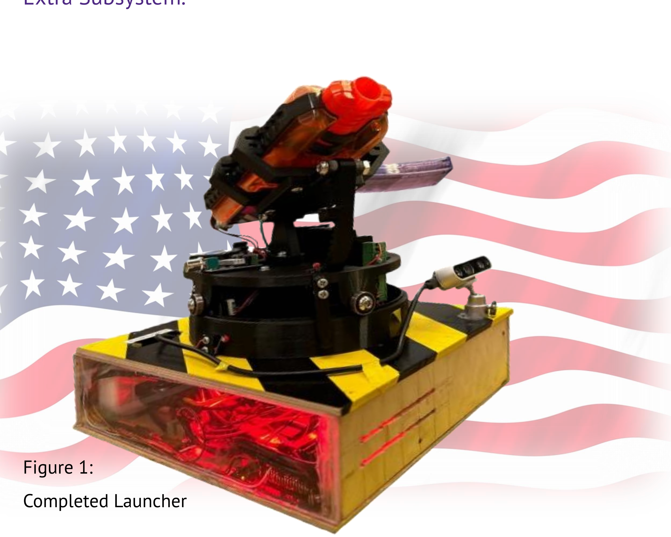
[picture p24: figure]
Figure 1: Completed Launcher

## Conclusion:

The team was able to successfully create the golf ball interceptor within DEVCOM’s specifications found in the rulebook. The team is overall pleased with the final result. The final budget is shown below.

Electrical Budget: | Combined Budget:

Detected Golf Balls

Processor: The Jetson Nano was chosen as the processor because of its capabilities. It gathers data from the camera and determines the line that the golf ball is traveling on.
Image Processing: Figure three shows the Intel RealSense camera’s detection abilities. It is detecting two golf balls on the gameboard and displays the distance of the coordinates.
Interceptor Controller: This subsystem controls all the mechanical portions of the design. It retrieves data from the Jetson Nano and converts it to movements for the motors to properly aim the launcher to one of the fifteen preset locations.
Extra: This system encompasses the mandatory pause switch as well as the lights and sounds that play before the interceptor fires at the golf ball.

## Experimentation

- The emergency stop, pause switch, lights, and firing sounds were implemented.
- The ECE and ME portions of the project were integrated successfully.
- The golf ball interceptor can successfully locate the ball, aim, and shoot.
- The launcher moves to fifteen different locations based on the line where the golf ball is detected.

Team: (Left to Right) Katie Swinea, Jonathan Neal, Finlay Patoto, Kevin Ulrich, Garrett Armstrong, Savannah Metzler

Figure 3: Camera Detecting Two Golf Balls

Team: | Total:
Electrical | 768.20
Mechanical | 290.00
| $1058.20

Figure 2: Final Projectile
(Nerf Bullet with hot glue stick inside)
Subsystems: | Total:
Power | 162.00
Extra | 35.19
Interceptor Controller | 27.60
Processor | 229.40
Camera (Sensor) | 314.00
Total: | $768.20

0

20

40

60

80

100

Hits | Misses | Total

Accuracy Trial

Accuracy: For the accuracy trials, a total of 80 trials were conducted. The total number of noticeable hits was 21. This sets the accuracy at 26%.

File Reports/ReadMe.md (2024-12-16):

# Reports

This directory includes the final version of our presentation, poster, project proposal, and conceptual design. For the experimental analysis, which contains the
results of our experimentation, go to the Experimental_Analysis directory. For the detailed design of each subsystem, go to the signoffs directory under
documentation. Lessons learned became a individual presentation and is not documented in the team's collective github.

## Completed Reports
The final version of the already completed reports are listed below.

1. [The project proposal](https://github.com/Katie-Swinea/Spring2024-Paper-Wad-Interceptor/blob/main/Reports/Project%20Proposal%20Revisions.pdf)
2. [Conceptual Design and Planning](https://github.com/Katie-Swinea/Spring2024-Paper-Wad-Interceptor/blob/main/Reports/Conceptual%20Design%20Final.pdf)

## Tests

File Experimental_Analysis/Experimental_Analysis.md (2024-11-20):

# Experimental Analysis

## Introduction 
The purpose of this report is to verify the requirements and constraints that impact the full functionality of the system and explain the prodecures used to validate them. The constraints for each subsystem were set and finialzed during the detail design phase of our senior design project. 

## Experimentation
Each subsystem will be divided into it's own section to make it easy to follow.

### Device Power

#### Constraints
| NO. | Constraint |
|-----|---|
| 1 | The power system shall be controlled by an emergency stop which will de-energize the mechanical system. This will shut off the motors which will not allow any projectiles to be fired. This will only be used if the system threatens peoples safety 
| 2 | The system shall be controlled by a power switch |

#### Results

#### 1 - Emergency Stop:

The system must have an emergency stop button that will completely de-energize the mechanical system. This means the processor and lights will remain on, while the motors and solenoid that make up the mechanical system will be completely off. 

To prove this constraint, the emergency stop was turned on and turned off 10 times. The results are listed below. 

| Trail Number | Mechanical System with E-Stop Pressed | Mechanical System with E-Stop Not Pressed |
|---|---|---|
| 1 | Off | On |
| 2 | Off | On |
| 3 | Off | On |
| 4 | Off | On | 
| 5 | Off | On |
| 6 | Off | On |
| 7 | Off | On |
| 8 | Off | On |
| 9 | Off | On |
| 10 | Off | On |

The below photos show how the emergency stop works and depicts that it is functioning correctly. 

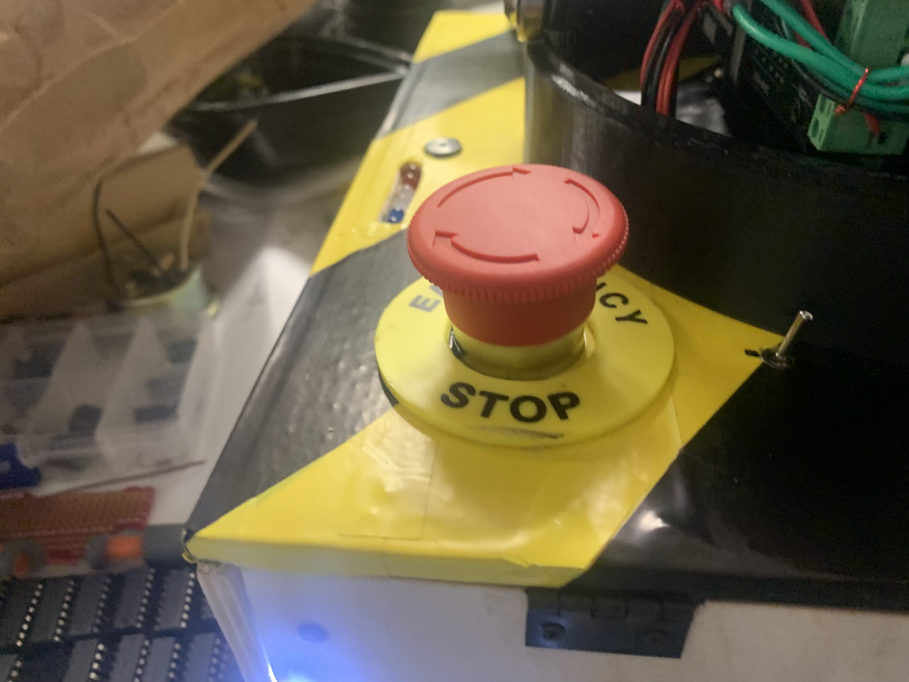
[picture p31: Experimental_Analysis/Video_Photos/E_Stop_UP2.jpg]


*E-Stop not pressed*

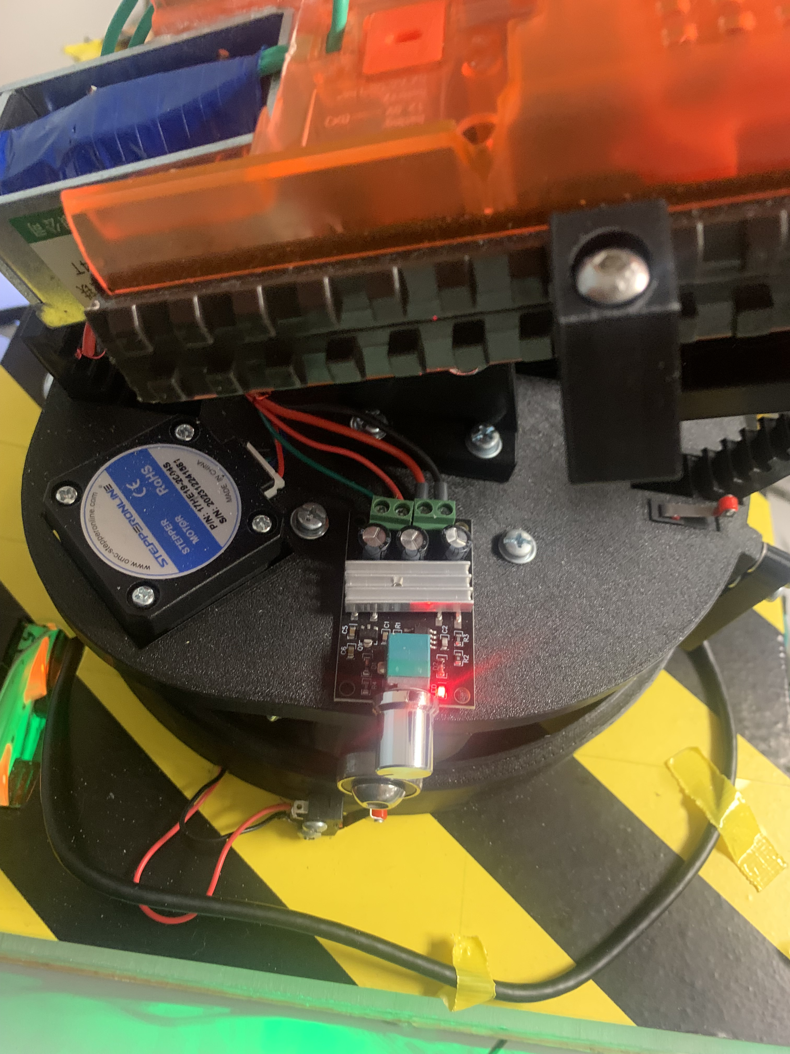
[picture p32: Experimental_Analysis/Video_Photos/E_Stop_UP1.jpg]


*E-Stop not pressed so system on*

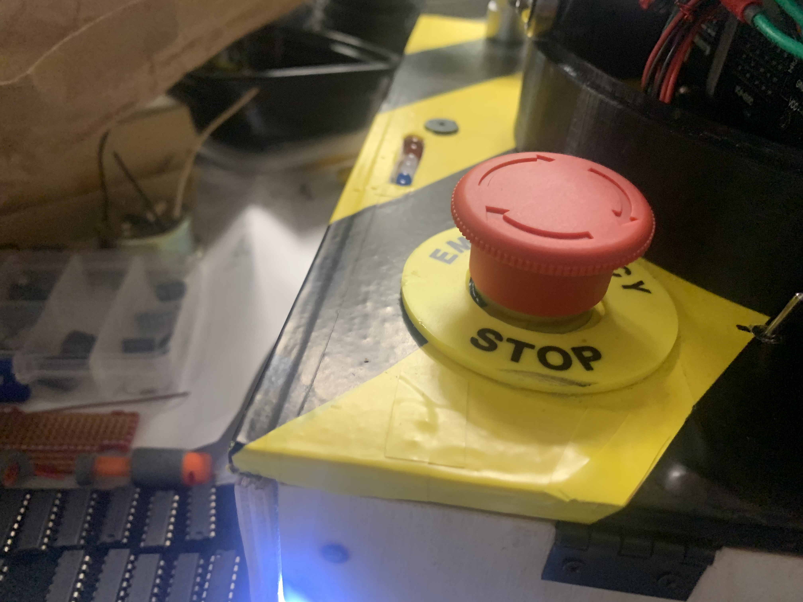
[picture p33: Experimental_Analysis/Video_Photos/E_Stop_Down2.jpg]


*E-Stop pressed*

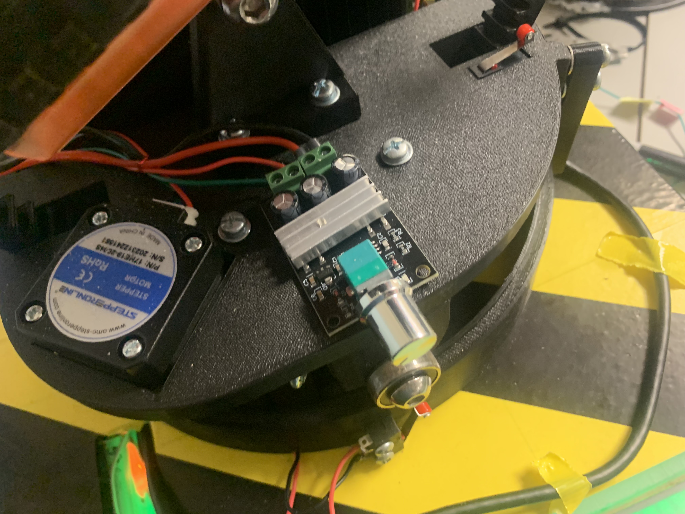
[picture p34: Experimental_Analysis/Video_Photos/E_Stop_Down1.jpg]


*E-Stop pressed so system off*

#### 2 – Power Switch 

The system must have a functioning power switch that turns the system on/off. For this system there are two switches. One that controls the mechanical system and one that controls the processor and light system. To test this, both switches were turned off and then on again to see if both successfully turn off and then on again. The results are listed below. 

| Trail Number | Mechanical Off | Mechanical On | Processor Off | Processor On |  
|---|---|---|---|---|
| 1 | Yes | Yes | Yes | Yes | 
| 2 | Yes | Yes | Yes | Yes | 
| 3 | Yes | Yes | Yes | Yes |  
| 4 | Yes | Yes | Yes | Yes | 
| 5 | Yes | Yes | Yes | Yes | 
| 6 | Yes | Yes | Yes | Yes |  
| 7 | Yes | Yes | Yes | Yes |  
| 8 | Yes | Yes | Yes | Yes | 
| 9 | Yes | Yes | Yes | Yes | 
| 10 | Yes | Yes | Yes | Yes | 

The below photos show the power switches functioning correctly. 

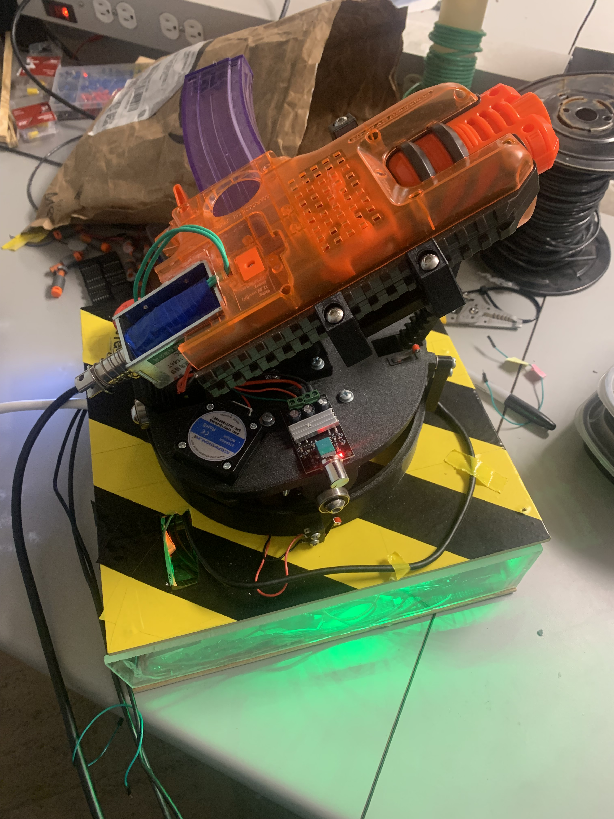
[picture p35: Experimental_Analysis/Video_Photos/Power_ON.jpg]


*Switch on so system is on*

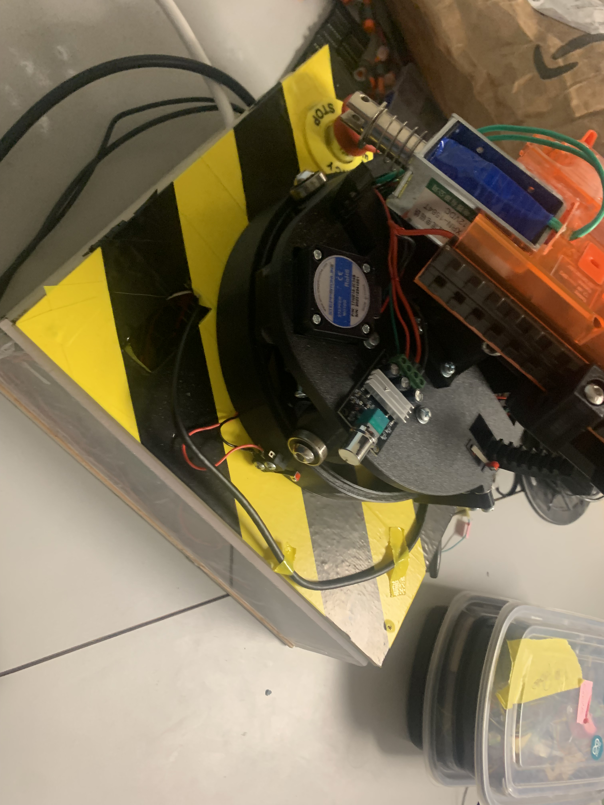
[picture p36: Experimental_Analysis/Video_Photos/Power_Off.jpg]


*Switch off so system is off*

### Extra

#### Constraints
| NO. | Constraint |
|-----|---|
| 1. |  The interceptor shall have a switch that sets the system into a pause state that will keep the interceptor from firing. |
| 2. | The voltage switched by the pause switch shall be 5V. |
| 3. | The interceptor must have lights that are bright enough to be seen by the judges approximately six and a half feet away, which is the longest length of the gameboard. Therefore the lights must have a candela rating greater than that of a fire alarm which is 15 cd. These lights must also emit a light that falls within the visual light spectrum of 380 to 720 nanometers. |
| 4. | The interceptor must make sounds before firing. The sounds will need to fall within the range of frequency humans can hear which is 20 to 20,000Hz. The volume, or loudness, must be 10db above the average of the room, which usually falls at 60 dB, in order for the judges to hear the sound. The sound must also not exceed 85dB for more than eight hours or it may cause hearing damage. |

#### Results

#### 1 - Pause Switch
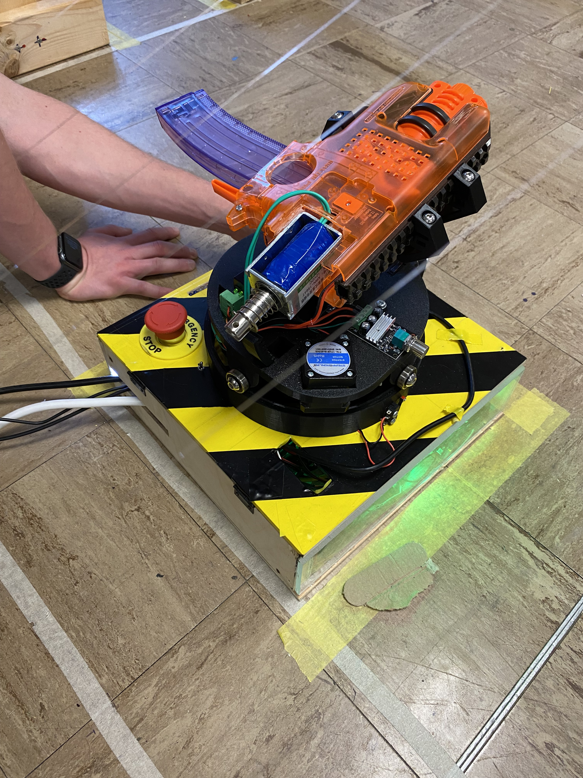
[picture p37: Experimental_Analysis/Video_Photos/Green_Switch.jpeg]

The image above shows the interceptor in the run state. Note the pause switch is to the right.

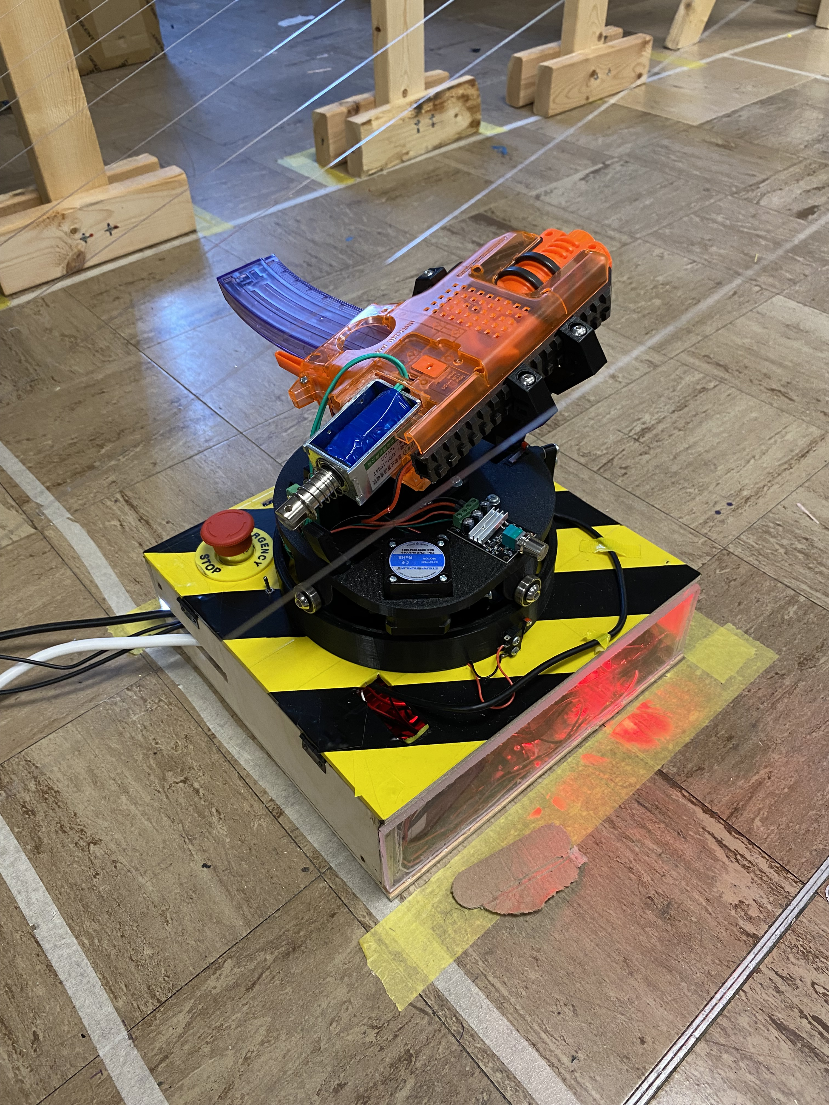
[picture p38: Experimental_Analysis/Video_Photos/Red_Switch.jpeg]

The image above shows the interceptor in the run state. Note the pause switch is to the left. 

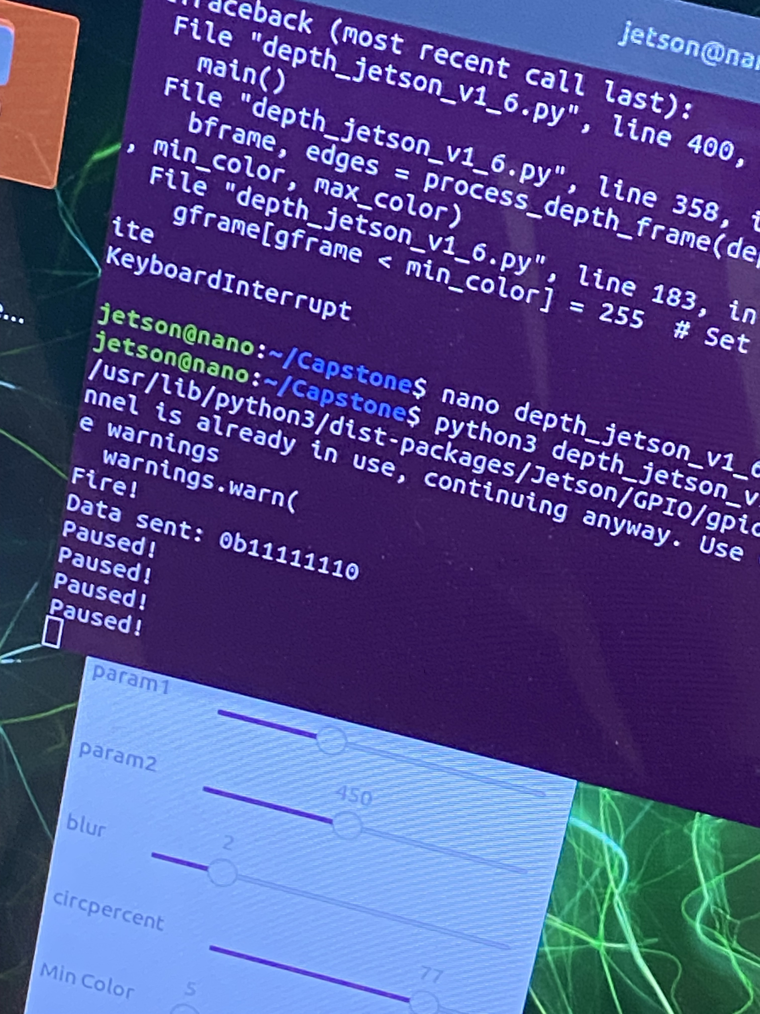
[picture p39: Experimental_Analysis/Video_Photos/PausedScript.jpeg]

The image above shows the running script and the outputs of the Jetson Nano in the terminal. When the Jetson prompts the interceptor to fire it can be seen that the script reads "Fire!". This shows that the interceptor can fire when the pause switch is off. When the pause switch is on and the interceptor is prompted to fire, the "Paused!" text can be seen and the interceptor does not fire. This shows that the interceptor is in the pause state. The following table shows the trials tested.

| NO. | Pause | Fire |
|-----|---|-----|
| 1. | Yes | No |
| 2. | No | Yes |
| 3. | Yes | No |
| 4. | No | Yes |
| 5. | No | Yes |
| 6. | Yes | No |
| 7. | No | Yes |
| 8. | Yes | No |
| 9. | Yes | No |
| 10. | No | Yes |

#### 2 - Pause Switch Voltage
The voltage switched by the pause switch was measured over the course of ten trials. All trial results are shown below. As can be seen the voltage switched by the pause switch is approximately 5V. 

| NO. | Result |
|-----|---|
| 1. | 5.05V |
| 2. | 5.05V |
| 3. | 5.05V |
| 4. | 5.05V |
| 5. | 5.05V |
| 6. | 5.05V |
| 7. | 5.05V |
| 8. | 5.05V |
| 9. | 5.05V |
| 10. | 5.05V |

#### 3 - Lights
The following images show that both the green and red lights can be seen from 6.5' away. 

#### Figure 1: Green LED's
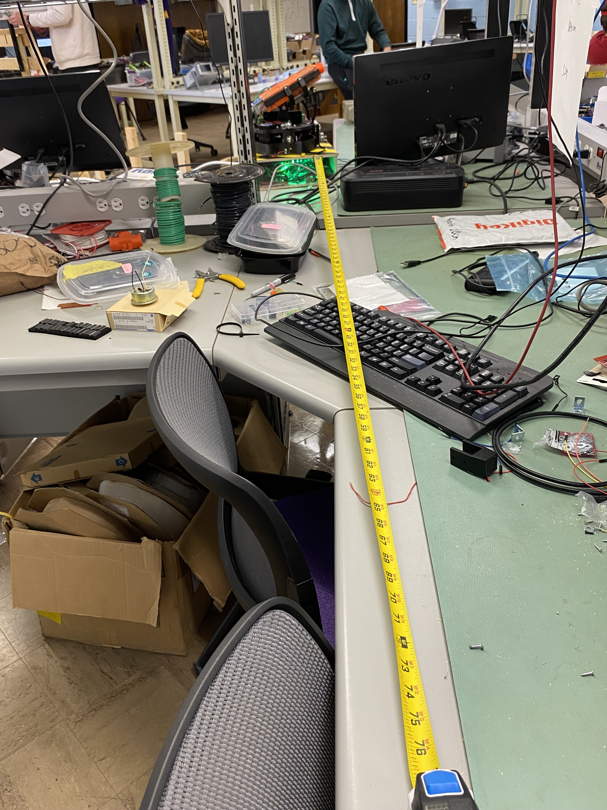
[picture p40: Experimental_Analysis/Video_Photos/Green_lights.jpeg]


#### Figure 2: Red LED's


#### 4 - Sounds
The interceptor does make sounds before firing. The sound is a frequency that humans can hear and it can be heard above the noise of the room and interceptor itself. The buzzer can be heard at the following YouTube link. [Link](https://youtube.com/shorts/tiVD-2daVd4)

### Image Processing
#### Constraints
| NO. | Constraint |
|-----|---|
| 1| Must be able to distinguish the golf ball from surroundings based on golf ball's shape and color |
| 2| Must be able to extract the x,y coordinates of the golf ball with an inch of accuracy to distinguish between the wires and variable height|
| 3| Must be able to receive the data and perform calculations in 500 ms to allow the interceptor time to aim and shoot based on the calculations|

#### Results

#### 1 - Golf Ball from Surroundings

The golf ball was able to be distinguished from the surroundings as seen in the picture below of the where the golf ball is and how it was detected: 





This shows that only the golf ball is fully detected with coordinates and a distance on the shape that was found. It uses the golf ball’s characteristics like size and shape to distinguish the ball. This was done at several different positions on each wire of the game board. However, false detections from the light above the gameboard are prominent. While a ball is on the gameboard, it is determined to be the real ball, and its coordinates are extracted as seen in the picture above. However, to obtain a better product, it would be ideal to reduce the noise in any conditions. Current ideas are being explored to remedy this further, but the ball is still able to be distinguished and intercepted when present.

The golf ball was placed at each of the 15 lines and then it was recorded if the ball was visible to the camera. The results are listed below. 

| Line Number | Was Detected by Camera |
|---|---|
| 1 | Yes |
| 2 | Yes |
| 3 | Yes |
| 4 | Yes |
| 5 | Yes |
| 6 | Yes |
| 7 | Yes |
| 8 | Yes |
| 9 | Yes |
| 10 | Yes |
| 11 | Yes |
| 12 | Yes |
| 13 | Yes |
| 14 | Yes |
| 15 | Yes |

#### 2 - x, y Coordinates of the Golf Ball

The depth camera has a FOV of about 86 by 57 degrees. The x and y coordinates are distinguishable as seen in the above experiment. At the same distance on line 7 and 8, the two balls are at 200 and 110 for 7 and 222 and 110 for 8. This gives a 22 pixel difference on the x coordinates. The FOV is 2 * tan (86/2) * distance. Distances is 75 inches in this case. Thus the FOV width in inches is 139.88. Each pixel per inch at this distance is 0.109. A 22 pixel distance means the lines are 2.40 inches apart. The measured distance between the lines is 3.25 inches. Thus the error is 0.85 inches and within the 1 inch error. This same process was done for multiple lines at multiple distances. 

| First Line | Second Line | Distance | Postion Error |
|---|---|---|---|
| 7 | 8 | 75 inches | 0.85 inches |
| 10 | 11 | 70 inches | 0.96 inches |
| 4 | 5 | 55 inches | 0.50 inches |
| 14 | 15 | 50 inches | 0.75 inches |
| 1 | 2 | 45 inches | 0.28 inches |
| 12 | 13 | 40 inches | 0.92 inches |
| 5 | 6 | 30 inches | 0.88 inches |

This shows that for many different positions the error does not get above an inch. While the changes in distance can vary due to the angle of the camera and the position that wire would be at on the camera, the accuracy of the position is still within an inch of the actual position. 

#### 3 - Perform Calculations in 500 ms

The ball will be able to be measured and calculated within 500 ms. It can be seen that several frames are received, detect the ball, and make calculations for interception. 

| Processing Time | Transfer Time | Additional Calculations | Total Time |
|---|---|---|---|
| 21.01 ms | 17.75 ms | 0.102 ms | 38.86 ms |
| 16.70 ms | 17.75 ms | 0.108 ms | 34.56 ms |
| 22.21 ms | 17.75 ms | 0.126 ms | 40.09 ms |
| 17.22 ms | 17.75 ms | 0.124 ms | 35.09 ms |
| 18.33 ms | 17.75 ms | 0.107 ms | 36.19 ms |
| 14.65 ms | 17.75 ms | 0.104 ms | 32.50 ms |
| 20.95 ms | 17.75 ms | 0.123 ms | 38.82 ms |
| 22.49 ms | 17.75 ms | 0.106 ms | 40.35 ms |
| 15.38 ms | 17.75 ms | 0.121 ms | 33.25 ms |

From the above values, it can be seen that the total processing time for a single frame is much lower than expected. Taking the worse frame time, 40.35 ms, and multiplying it by 3 to get the amount of frames needed for velocity and acceleration calculations gives a total time of 121.05 ms. This allows for error checking to add an additional three frames to determine any false detections and then do the calculations. This would give a total time of 242.10 ms. This is well within the 500 ms limit that was given. This also allows for the time of one second from the release of the ball to the ‘kill-zone’ to be achievable. The time for positioning and firing the interceptor is about 500 ms giving a total interception time of 742.10 ms. It is important to note the kill zone is 21 inches from the tip of the gun, allowing time for the projectile to fire and make contact with the golf ball. 

### Interceptor Controller

#### Constraints

| NO. | Constraint |
|-----|---|
|1|The Interceptor Controller shall move firing mechanism to 1 of 30 pre set locations |
|2|Must maintain safe firing speed and distance|
|3|Must change position before incoming object enters the "kill zone"|

#### Results
#### 1 - 1-30 Pre-Set Locations
For minimal functional prototype we only have 15 of the 30 set positions at this time.
|Line|Height| Movement|
|---|--|-----|
|1|2|Yes|
|2|2|Yes|
|3|2|Yes|
|4|2|Yes|
|5|2|Yes|
|6|2|Yes|
|7|2|Yes|
|8|2|Yes|
|9|2|Yes|
|10|2|Yes|
|11|2|Yes|
|12|2|Yes|
|13|2|Yes|
|14|2|Yes|
|15|2|Yes|

#### 2 - Safe Firing Speed/ Distance

#### 3 - Kill Zone
The firing mechanism must change its position before the golf ball enters the kill zone. Like the Pre-Set location Constraint we only have 15 out of the 30 set positions.
| Line #'s kill zone | Movement |
|---|----|
|1|Yes|
|2|Yes|
|3|Yes|
|4|Yes|
|5|Yes|
|6|Yes|
|7|Yes|
|8|Yes|
|9|Yes|
|10|Yes|
|11|Yes|
|12|Yes|
|13|Yes|
|14|Yes|
|15|Yes|

### Sensor Subsystem

#### Constraints

| NO. | Constraint |
|-----|---|
| 1 | The sensor shall be able to retrieve at least 3 data points within 0.0667s in order to calculate speed which allows for maximum time for calculations given the constraints of the image processing system  |
| 2 | The sensor shall have a FOV that is wider than 56" from 6' away which is the width of anchor 2 and the length of the gameboard |

#### Results

#### 1 - Data Points

We are only using the depth camera portion of the Intel D435 camera which has a frame rate of 90 frames per second. At that speed we are able to get a new frame of data points every 0.011 seconds. This means that we are able to get 3 frames of data within 0.033 seconds which is lower than the 0.0667 second constraint.:

~~~ math
1 / 90 = 0.0111
~~~

~~~ math
0.011 * 3 = 0.0333
~~~

#### 2 - Field of View

As you can see in the photo below you can clearly see the entirety of anchor 2 plus some. Therefore it passes this constraint.

Picture of Anchor 2

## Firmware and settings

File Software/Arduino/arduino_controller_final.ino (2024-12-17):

// Define stepper motor connections:
#define dirPin 2
#define stepPin 3
#define dirPin1 4
#define stepPin1 5
#define solenoidPin 6
#define motorInterfaceType 1
#include <ezButton.h>
#include <AccelStepper.h>
#include <Wire.h>
#include <avr/wdt.h>

#define MAX_POSITION 0x7FFFFFFF  // maximum of position we can set (long type)

ezButton limitSwitch(A0);  // create ezButton object that attach to pin A0;
ezButton limitSwitch1(A1);
ezButton limitSwitch2(A2);
ezButton limitSwitch3(A3);

AccelStepper stepper = AccelStepper(motorInterfaceType, stepPin, dirPin);
AccelStepper stepper1 = AccelStepper(motorInterfaceType, stepPin1, dirPin1);

// Array for X motor (stepper1), handling X positions (0 to 31)
/*int motorStepsX[32] = {
  0, 17.419, 34.838, 52.257, 69.676, 87.095, 104.514, 121.933, 139.352, 156.771,
  174.19, 191.609, 209.028, 226.447, 243.866, 261.285, 278.704, 296.123, 313.542, 330.961,
  348.38, 365.799, 383.218, 400.637, 418.056, 435.475, 452.894, 470.313, 487.732, 505.151,
  522.57, 539.989
};*/
int motorStepsX[32] = {
  53, 50, 47, 43, 38, 36, 33, 31, 27, 22,
  18, 16, 13, 11, 8, 0, 0, 0, 0, 0,
  0, 0, 0, 0, 0, 0, 0, 0, 0, 0,
  0, 0
};

// Array for Y motor (stepper), handling Y positions (0 to 3)
static int motorStepsY[4] = {
  0, 20, 40, 60
};

// Bools for ME
bool isStopped = false;
bool isStopped1 = false;
bool isBothStopped = false;
bool fire = false;
bool fired = true;  // MY BOOL NO TOUCHY
bool inTheMiddle = false;
bool aimbot = false;
bool isAtTarget = false;
bool atTarget = false;
bool atTarget1 = false;
int middle = 1200;
int middle1 = 200;
int target = 0;
int target1 = 0;
int i = 0;
int j = 0;

// Variables for received X/Y position
int xPosition = -1;
int yPosition = -1;
int delayFire = -1;

void setup() {
  Serial.begin(9600);

  // Declare pins as output:
  pinMode(stepPin, OUTPUT);
  pinMode(dirPin, OUTPUT);
  pinMode(stepPin1, OUTPUT);
  pinMode(dirPin1, OUTPUT);

  // Set the spinning direction CW/CCW:
  digitalWrite(dirPin, LOW);
  digitalWrite(dirPin1, HIGH);

  pinMode(solenoidPin, OUTPUT);

  limitSwitch.setDebounceTime(10);
  limitSwitch1.setDebounceTime(10);
  limitSwitch2.setDebounceTime(100);
  limitSwitch3.setDebounceTime(100);

  stepper.setMaxSpeed(6000);
  stepper.setAcceleration(4000);
  stepper1.setMaxSpeed(6000);
  stepper1.setAcceleration(4000);

  // Finn custom
  pinMode(13, OUTPUT);
  Wire.begin(8);                 // Initialize I2C with address 8
  Wire.onReceive(receiveEvent);  // Register receive event
  Serial.begin(9600);
}

void(* resetFunc) (void) = 0;
void loop() {

  if (fire) {
    // Wait to fire based on ms
    delay((delayFire));

    digitalWrite(solenoidPin, HIGH);  //Switch Solenoid ON
    delay(1000);                      //Wait 1 Second
    digitalWrite(solenoidPin, LOW);   //Switch Solenoid OFF
    delay(1000);                      //Wait 1 Second
    fired = true;
    fire = false;

    digitalWrite(dirPin, LOW);
    digitalWrite(dirPin1, HIGH);

    resetFunc();
  }

  if (isBothStopped == false) {
    if (isStopped == false) {
      // These four lines result in 1 step:
      digitalWrite(stepPin, HIGH);
      delayMicroseconds(500);
      digitalWrite(stepPin, LOW);
      delayMicroseconds(500);
    }
    if (isStopped1 == false) {
      digitalWrite(stepPin1, LOW);
      delayMicroseconds(500);
      digitalWrite(stepPin1, HIGH);
      delayMicroseconds(500);
    }

    limitSwitch.loop();  // MUST call the loop() function first

    if (limitSwitch.isPressed()) {
      digitalWrite(dirPin, HIGH);
      isStopped = true;
      stepper.setCurrentPosition(0);  // Reset motor position to 0
    }

    limitSwitch1.loop();  // MUST call the loop() function first

    if (limitSwitch1.isPressed()) {
      digitalWrite(dirPin1, LOW);
      isStopped1 = true;
      stepper1.setCurrentPosition(0);  // Reset motor position to 0
    }
    if (isStopped == true && isStopped1 == true) {
      isBothStopped = true;
    }

    stepper.run();
    return;
  }
  if (isBothStopped == true && fired) {
    // Set the target position:
    stepper.moveTo(100);
    // Run to target position with set speed and acceleration/deceleration:
    stepper.runToPosition();
    stepper.setCurrentPosition(0);  // Reset motor position to 0

    // Set the target position:
    stepper1.moveTo(-280);
    // Run to target position with set speed and acceleration/deceleration:
    stepper1.runToPosition();
    stepper1.setCurrentPosition(0);  // Reset motor position to 0
    isBothStopped = false;

    fired = false;
  }

  // Move steppers to received X/Y positions
  if ((yPosition >= 0) && (xPosition >= 0)) {
    // KEEP THIS PRINT STATEMENT OR YOU WILL BREAK THIS CODE COMPLETELY
    Serial.println(" ");
    Serial.println(motorStepsY[yPosition], DEC);  // Print X in decimal
    Serial.println(motorStepsX[xPosition], DEC);  // Print X in decimal

    if (((yPosition * 20) + 100) > 160 || ((yPosition * 20) + 100) < 100) {
      Serial.print("yPos Bad!: ");
      //Serial.println(((yPosition * 20) + 100), DEC);  // Print X in decimal
      Serial.println(yPosition, DEC);  // Print X in decimal
      Serial.println(xPosition, DEC);  // Print X in decimal
      stepper.moveTo(0);             // Mapping X to stepper position, adjust the multiplier as needed
    } else { 
      stepper.moveTo(((yPosition * 20)));  // Mapping X to stepper position, adjust the multiplier as needed
    }

    // Move X motor (stepper1) using the X position array
    stepper1.moveTo(-(motorStepsX[xPosition]*8) + 280);  // X motor moves based on xPosition
    //stepper1.moveTo(-((xPosition * 8)) + 280 - 248);  // X motor moves based on xPosition

    stepper.runToPosition();
    stepper1.runToPosition();

    xPosition = -1;
    yPosition = -1;
  }
}

void receiveEvent(int howMany) {
  while (Wire.available()) {
    byte receivedData = Wire.read();  // Read incoming data

    // Check if MSB is 1
    if (receivedData & 0b10000000) {  // Check MSB
      // MSB is 1, do "fire" and print remaining bits
      Serial.println("fire");

      // Print remaining bits (7 bits)
      byte remainingBits = receivedData & 0b01111111;  // Mask to get remaining bits
      Serial.print("Remaining Bits: ");
      Serial.println(remainingBits, DEC);  // Print in decimal

      byte delayFire_byte = receivedData & 0b01111111;

      // add calculation for delay in ms
      delayFire = delayFire_byte;

      fire = true;

    } else {
      // MSB is 0, extract the next two bits as Y and print X position
      byte Y = (receivedData >> 5) & 0b00000011;  // Extract bits 6 and 7 for Y
      byte X = receivedData & 0b00011111;         // Get the remaining bits as X (bits 0-4)

      // Store received X and Y positions
      xPosition = X;
      yPosition = Y;
    }
  }
}

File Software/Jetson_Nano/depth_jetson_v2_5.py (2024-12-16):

import time
import numpy as np
import cv2
import Jetson.GPIO as GPIO  # Import the GPIO library
import pyrealsense2 as rs  # RealSense library
from typing import Tuple
import subprocess
import sys
import threading
import os
import smbus2
import time
import math

# I2C bus (1 for Jetson Nano)
bus = smbus2.SMBus(1)

# Arduino I2C address
slave_address = 0x08  # Ensure this matches your Arduino address (0x08 is 8 in hexadecimal)

# Pins for JettyNano
SCRIPT_RUNNING_PIN = 12
SCRIPT_PAUSE_PIN = 18
BUZZER_PIN = 37

# Data keeping
frame_data = []  # Array to store the frame information
processing_times = []  # List to track frame processing times
frame_count = 3
frame_valid_count = 0
frame_similarity_threshold = 0.1
frame_range_threshold = 25

# Data Sending
data_interval = 10
check_interval = 0

# Pass through code
def nothing(_):
    pass

# Look up table for positioning
lookup_table = {
    # Table structure:
    # DIST, X, Y: LINE
    
    # Info at 75" -- NOT CONFIRMED-- FINLAY CONFRIMED WITH NEW CAMERA
    (75, 71, 120): 1,
    (75, 91, 120): 2,
    (75, 113, 120): 3,
    (75, 138, 120): 4,
    (75, 158, 121): 5,
    (75, 178, 122): 6,
    (75, 199, 124): 7,
    (75, 222, 128): 8,
    (75, 242, 125): 9,
    (75, 261, 128): 10,
    (75, 283, 129): 11,
    (75, 303, 129): 12,
    (75, 324, 129): 13,
    (75, 345, 128): 14,
    (75, 370, 128): 15,

    # Info at 70" -- NOT CONFIRMED-- FINLAY CONFRIMED WITH NEW CAMERA
    (70, 70, 118): 1,
    (70, 90, 118): 2,
    (70, 112, 118): 3,
    (70, 137, 118): 4,
    (70, 159, 115): 5,
    (70, 180, 121): 6,
    (70, 200, 118): 7,
    (70, 223, 120): 8,
    (70, 245, 122): 9,
    (70, 266, 120): 10,
    (70, 287, 122): 11,
    (70, 309, 123): 12,
    (70, 331, 122): 13,
    (70, 352, 122): 14,
    (70, 374, 120): 15,
    
    # Info at 65" -- NOT CONFRIMED-- FINLAY CONFRIMED WITH NEW CAMERA
    (65, 73, 112): 1,
    (65, 93, 112): 2,
    (65, 115, 94): 3,
    (65, 140, 112): 4,
    (65, 158, 114): 5,
    (65, 180, 112): 6,
    (65, 204, 113): 7,
    (65, 225, 114): 8,
    (65, 249, 114): 9,
    (65, 268, 115): 10,
    (65, 292, 117): 11,
    (65, 313, 118): 12,
    (65, 337, 117): 13,
    (65, 360, 116): 14,
    (65, 377, 118): 15,

    # Info at 60" -- FINLAY CONFRIMED WITH NEW CAMERA
    (60, 61, 106): 1,
    (60, 85, 110): 2,
    (60, 107, 108): 3,
    (60, 132, 109): 4,
    (60, 153, 109): 5,
    (60, 176, 108): 6,
    (60, 200, 110): 7,
    (60, 222, 109): 8,
    (60, 244, 108): 9,
    (60, 279, 109): 10,
    (60, 291, 109): 11,
    (60, 317, 105): 12,
    (60, 340, 110): 13,
    (60, 359, 110): 14,
    (60, 383, 108): 15,

    # Info at 55" -- FINLAY CONFRIMED WITH NEW CAMERA
    (55, 57, 95): 1,
    (55, 81, 99): 2,
    (55, 105, 96): 3,
    (55, 131, 94): 4,
    (55, 154, 96): 5,
    (55, 178, 97): 6,
    (55, 203, 98): 7,
    (55, 225, 98): 8,
    (55, 250, 95): 9,
    (55, 275, 95): 10,
    (55, 300, 95): 11,
    (55, 324, 95): 12,
    (55, 349, 99): 13,
    (55, 372, 100): 14,
    (55, 393, 100): 15,

    # Info at 50" -- FINLAY CONFRIMED WITH NEW CAMERA
    (50, 53, 84): 1,
    (50, 76, 87): 2,
    (50, 102, 83): 3,
    (50, 130, 84): 4,
    (50, 154, 88): 5,
    (50, 179, 87): 6,
    (50, 207, 88): 7,
    (50, 230, 88): 8,
    (50, 255, 87): 9,
    (50, 282, 88): 10,
    (50, 307, 88): 11,
    (50, 332, 88): 12,
    (50, 359, 90): 13,
    (50, 383, 93): 14,
    (50, 403, 89): 15,

    # Info at 45" -- FINLAY CONFRIMED WITH NEW CAMERA
    (45, 47, 72): 1,
    (45, 72, 77): 2,
    (45, 101, 74): 3,
    (45, 129, 73): 4,
    (45, 151, 79): 5,
    (45, 180, 78): 6,
    (45, 207, 81): 7,
    (45, 232, 78): 8,
    (45, 260, 77): 9,
    (45, 288, 77): 10,
    (45, 315, 75): 11,
    (45, 340, 77): 12,
    (45, 370, 77): 13,
    (45, 396, 80): 14,
    (45, 423, 74): 15,

    # Info at 40" -- FINLAY CONFRIMED WITH NEW CAMERA
    (40, 42, 59): 1,
    (40, 68, 61): 2,
    (40, 95, 60): 3,
    (40, 127, 62): 4,
    (40, 153, 68): 5,
    (40, 181, 65): 6,
    (40, 211, 66): 7,
    (40, 237, 65): 8,
    (40, 265, 65): 9,
    (40, 295, 66): 10,
    (40, 324, 62): 11,
    (40, 351, 62): 12,
    (40, 383, 63): 13,
    (40, 410, 66): 14,
    (40, 437, 60): 15,

    # Info at 35" -- FINLAY CONFRIMED WITH NEW CAMERA
    (35, 31, 37): 1,
    (35, 60, 40): 2,
    (35, 90, 35): 3,
    (35, 125, 36): 4,
    (35, 153, 45): 5,
    (35, 182, 41): 6,
    (35, 217, 41): 7,
    (35, 245, 41): 8,
    (35, 275, 40): 9,
    (35, 308, 40): 10,
    (35, 341, 37): 11,
    (35, 369, 39): 12,
    (35, 403, 42): 13,
    (35, 430, 48): 14,
    (35, 459, 42): 15,

    # Info at 30" -- FINLAY CONFRIMED WITH NEW CAMERA
    (30, 17, 22): 1,
    (30, 53, 19): 2,
    (30, 84, 12): 3,
    (30, 123, 12): 4,
    (30, 153, 18): 5,
    (30, 186, 13): 6,
    (30, 225, 14): 7,
    (30, 255, 15): 8,
    (30, 288, 14): 9,
    (30, 325, 15): 10,
    (30, 356, 19): 11,
    (30, 388, 15): 12,
    (30, 426, 19): 13,
    (30, 460, 20): 14,
    (30, 496, 17): 15,
}

# Function to find closet match Line inside the saved data array.
def find_line(distance: float, x: float, y: float) -> int:
    # Sort by closest distance first, then by closest x, and finally closest y
    sorted_entries = sorted(
        lookup_table.keys(),
        key=lambda k: (abs(k[0] - distance), abs(k[1] - x), abs(k[2] - y))
    )
    
    # Retrieve the int value corresponding to the closest (distance, x, y)
    closest_key = sorted_entries[0]
    return lookup_table[closest_key]

def calculate_intercept_time(initial_position, target_position, initial_velocity, acceleration):
    if acceleration == 0:
        # Avoid division by zero; use constant velocity formula instead
        if initial_velocity == 0:
            return 0  # Object won't move without velocity or acceleration
        return (target_position - initial_position) / initial_velocity
    
    # Coefficients of the quadratic equation at^2 + bt + c = 0
    A = 0.5 * acceleration
    B = initial_velocity
    C = initial_position - target_position

    # Calculate the discriminant
    discriminant = B**2 - 4 * A * C
    
    # Check if the discriminant is non-negative, else return None for no real solution
    if discriminant < 0:
        return 0  # No real solutions (complex roots)

    # Calculate both solutions for time
    time1 = (-B + math.sqrt(discriminant)) / (2 * A)
    time2 = (-B - math.sqrt(discriminant)) / (2 * A)

    # Filter out negative time values and return the smallest positive one
    times = [t for t in [time1, time2] if t >= 0]
    return min(times) if times else 0  # Return the positive time if it exists, else None

def Buzz(delay):
    GPIO.output(BUZZER_PIN, GPIO.HIGH)  # Turn on buzzer
    time.sleep(delay)  # Keep it on for half the period
    GPIO.output(BUZZER_PIN, GPIO.LOW)  # Turn on buzzer
    time.sleep(delay)  # Keep it on for half the period
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

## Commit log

2024-07-14 Update Flow Chart to Show Detection Algorithms
2024-08-27 Update Extra.md
    Need to address switch
2024-09-04 Extra (#13)
    * Extra.md
    * Extra.md
    * Extra.md
    Pasted formatting
    * Update Extra.md
    Added
    * Add files via upload
    * Update Extra.md
    * Update Extra.md
    * Update Extra.md
    idk
    * Add files via upload
    * Update Extra.md
    Added more stuff
    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
    [PauseSwitch-B_Cu.gbl, PauseSwitch-B_Mask.gbs, PauseSwitch-B_Paste.gbp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]
2024-11-19 Update with partial sensor subsystem
2024-11-20 Added sensor_fov.png
